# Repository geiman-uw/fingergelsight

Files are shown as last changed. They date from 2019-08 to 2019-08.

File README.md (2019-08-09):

# Assistive Finger GelSight

Words about the thing

## Table of Contents

* [Manufacture](#manufacture)  
  * [Supplies required](#supplies)  
  * [Core procedure](#coreprocedure)  
  * [Electronics procedure](#electronicsprocedure)  
  * [Assembly and installation](#aandi)  
* [Usage](#usage)
* [Capabilities](#capabilities)

## Manufacture

#### Supplies required<a name="supplies"/>
###### Chemicals
* Ease Release 200
* Silicones, Inc. XP-565
* Yellow Print-On Silicone Ink
* Print-On Silicone Ink diluent
* ?mm transparent acrylic
* Gray Print-On Silicone Ink
* Acrylic glue
<!--* Silicone glue-->
###### Other supplies
* Clear PLA 3D printer filament
* Petri dishes
* Pour boats
* Popsicle mixing sticks
* Pipets
* Needle-tip bottle

#### Equipment required
* Fume hood *(if available)*
* Vacuum chamber
* Toaster oven
* 3D printer
* Laser cutter

A vacuum chamber and toaster oven have been stored in ECE B031 ("silicone lab"), but check with the current project owner for the current location. There are multiple makerspaces at UW which have 3D printers and laser cutters; the two most accessible are the MILL in McCarty Hall and CoMotion Makerspace in Fluke Hall.

### Core procedure<a name="coreprocedure"/>  
Notes:
* You may find it most efficient to make 4-8 cores at a time with this procedure.
* Mix silicones in a pour boat using a popsicle stick. Use popsicle sticks to portion more viscous materials such as silicone base, and pipets to portion less viscous materials such as activator and diluent. Never use the same pipet or popsicle stick for different materials. 
* PLA parts shrink when exposed to heat. If you plan to modify the core, make your part approximately 5% bigger than the intended final size in order to account for this.
#### 1. Silicone lab
* __Cast transparent gel silicone__: After ensuring petri dish is free of dust, spray petri dish with Ease Release 200. Mix 17-18g XP-565, then pour 15g into dish. Vacuum until no bubbles remain, then heat on warm for 10 min.
* __Add yellow layer__: Starting with a 1g of yellow Silicone Ink, mix in a 1:10:60 activator:ink:diluent ratio. The resulting mixture should be approximately the consistency of chocolate milk. Pour in a thin even layer over the XP-565 petri dish. The layer should be as thin as possible, so you will not use all of the yellow silicone. Heat the dish on warm for 15 min.

#### 2. Makerspace
All production files can be found in `finger_gelsight_production`.
* **Print parts**: Print `gelsight_shell.stl` and `gelsight_piece.stl` in opaque PLA. Print `gelsight_corefilled_103.stl` open side up in clear PLA with 0.2mm layer height, raft, and no support.
* **Laser cut acrylic**: Laser cut `gelsight_corefilled_acrylic.stl` with vector set to *8s 100p 100f*.
* **Laser cut and engrave gel**: Remove transparent/yellow silicone from petri dish and place yellow-side up in laser cutter. Laser cut `gelsight_gelpattern_5x14.ai` with raster set to *11s 4p 50f* and vector set to *5s 75p 50f*.

#### 3. Silicone lab
* __Cast transparent core silicone__: Mix enough XP-565 to fill the prepared cores, and vacuum in pour boat until most bubbles are gone. 
* __Glue acrylic into core__: Using a needle-tip bottle, apply acrylic glue to the inside of the cores and place acrylic. Make sure the glue gets all the way around the edges, otherwise the silicone will seep past the acrylic and obstruct the camera lens later.
* __Fill core with silicone__: Carefully fill each core with silicone (at or below edge; do not overflow) and vacuum until no bubbles remain, then heat on warm for 5 min. 
* __Add protection layer__: Starting with 0.5g of gray Silicone Ink, mix in a 1:10:40 activator:ink:diluent ratio. The resulting mixture should be somewhat thicker than chocolate milk. Cover the bottom of each cut-out gel with electrical tape, making sure there are no bubbles where gray silicone could seep under the gel. Place dot-side up in a petri dish. Using a pipet, cover each gel in gray silicone mix, making sure all untaped sides are covered. 
* __Attach gel to core__: Once cores have cooled, spread a thin layer of mixed XP-565 on each core. Gently place gel on XP-565 layer, being careful to avoid introducing bubbles. Heat on warm for 5 min.

### Electronics procedure<a name="electronicsprocedure"/>
Wire two Adafruit LED sequins in parallel. Cut and strip a USB cable and solder each LED lead to the appropriate USB cable wire.
[images]

### Assembly and installation<a name="aandi"/>
Tap core and shell holes with M2 tap. Attach LEDs to core with transperent double sided tape. Screw core into shell. Attach camera to core with double sided tape, being careful not to force the lens into the hole. Tape wires to shell to provide more stability.

On Kinova hand remove original KG-2 distal phalanxes, being careful not to stretch rubber excessively. Place Finger GelSight and screw in shell piece. Continue as if installing original Kinova distal phalanx. Plug both USBs into the wrist controller. The fingers are now ready to use.

## Usage

## Capabilities

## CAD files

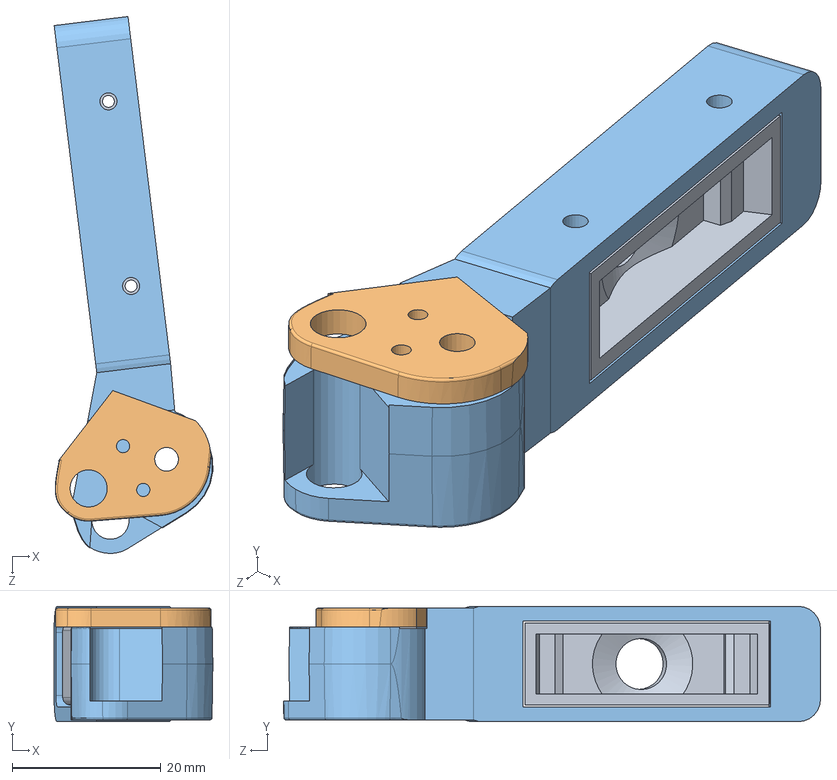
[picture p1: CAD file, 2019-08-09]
finger_gelsight_assembly/gripper_fingerassembly.sldasm
21.3 x 15.5 x 72.2 mm
gelsight_shell
gelsight_piece
gelsight_corefilled

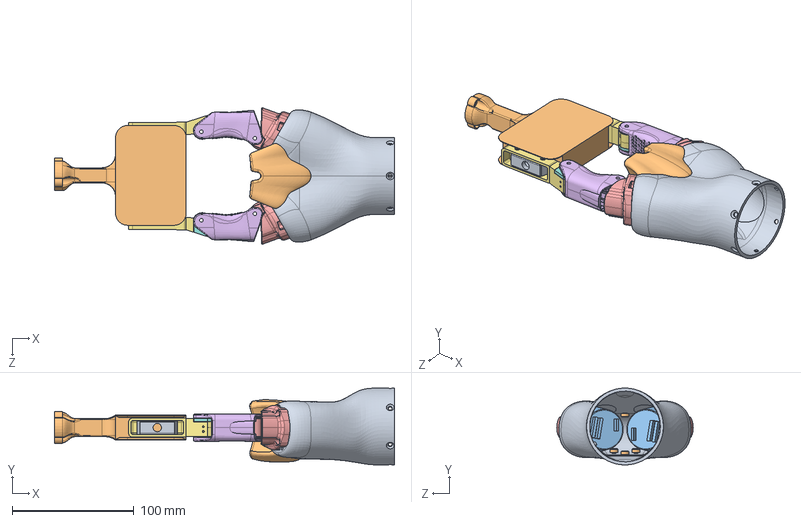
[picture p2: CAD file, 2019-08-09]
finger_gelsight_assembly/gripper_assembly.SLDASM
278.9 x 63.0 x 112.0 mm
gripper_handshell
gripper_handfront
actuator_dummy x 2
actuator_cup x 2
gripper_fingershroud x 2
gripper_middlephalanx x 2
gelsight_shell x 2
gelsight_piece x 2
gelsight_corefilled x 2
forkholder

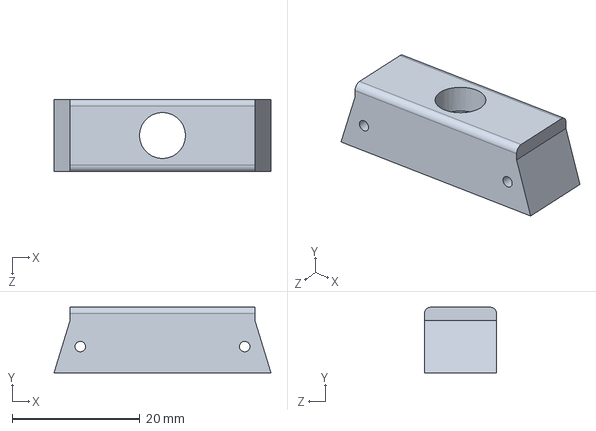
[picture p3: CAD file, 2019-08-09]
finger_gelsight_production/gelsight_corefilled_103.SLDPRT
34.0 x 10.3 x 11.3 mm

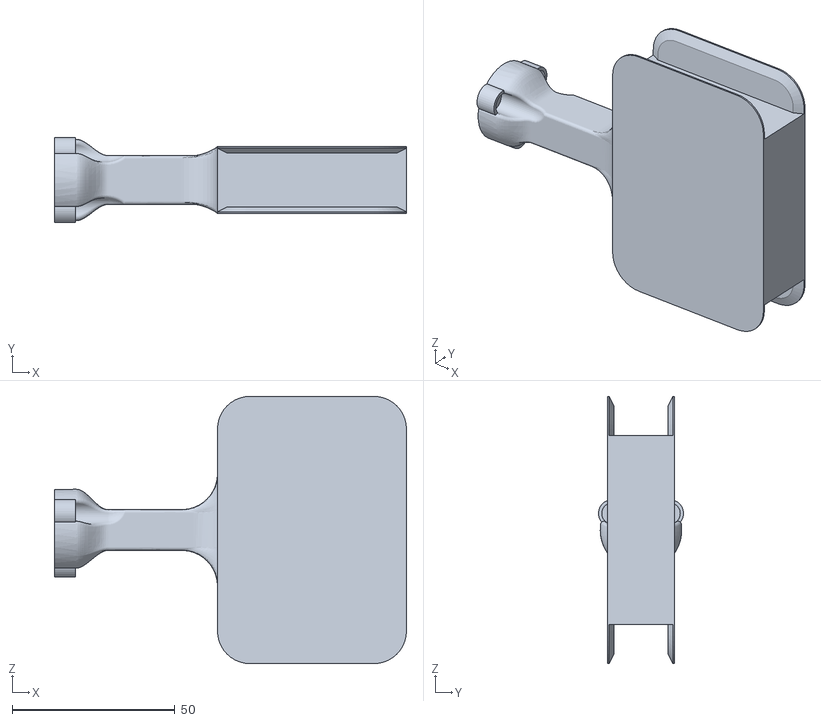
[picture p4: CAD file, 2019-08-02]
finger_gelsight_production/forkholder.STL
108.0 x 26.1 x 82.0

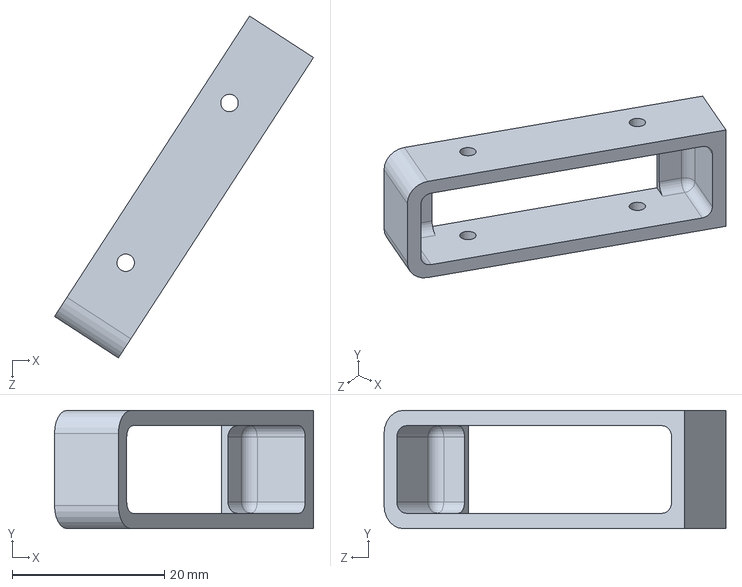
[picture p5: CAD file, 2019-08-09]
finger_gelsight_assembly/Body5.sldprt
34.0 x 15.5 x 44.9 mm

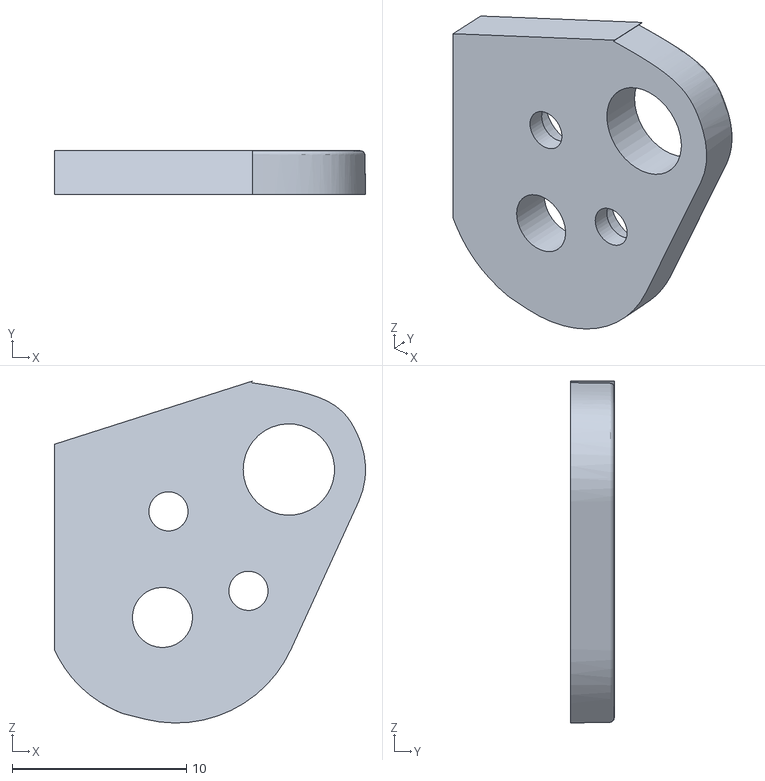
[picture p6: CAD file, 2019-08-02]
finger_gelsight_production/gelsight_piece.STL
17.9 x 2.50 x 19.7

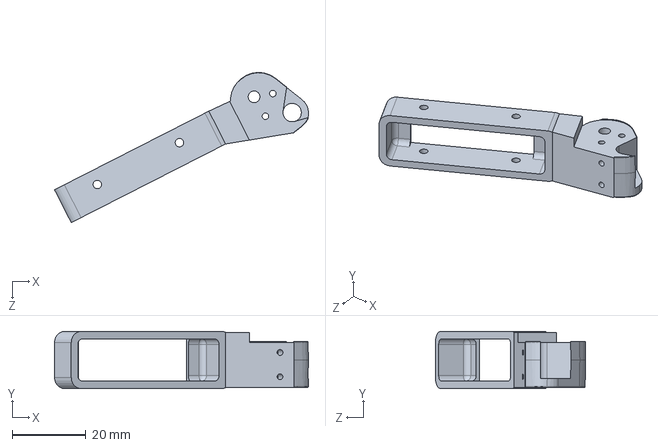
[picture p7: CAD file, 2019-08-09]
finger_gelsight_assembly/gelsight_shell.sldprt
68.9 x 15.5 x 40.8 mm

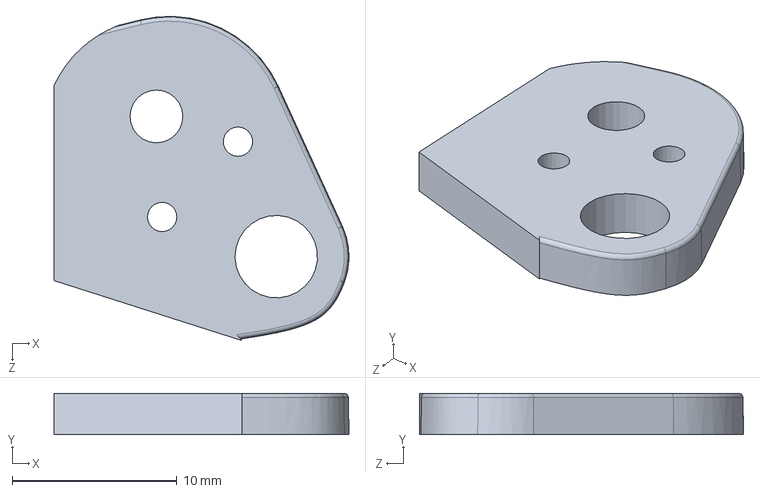
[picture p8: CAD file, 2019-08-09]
finger_gelsight_assembly/gelsight_piece.sldprt
17.9 x 2.50 x 19.6 mm

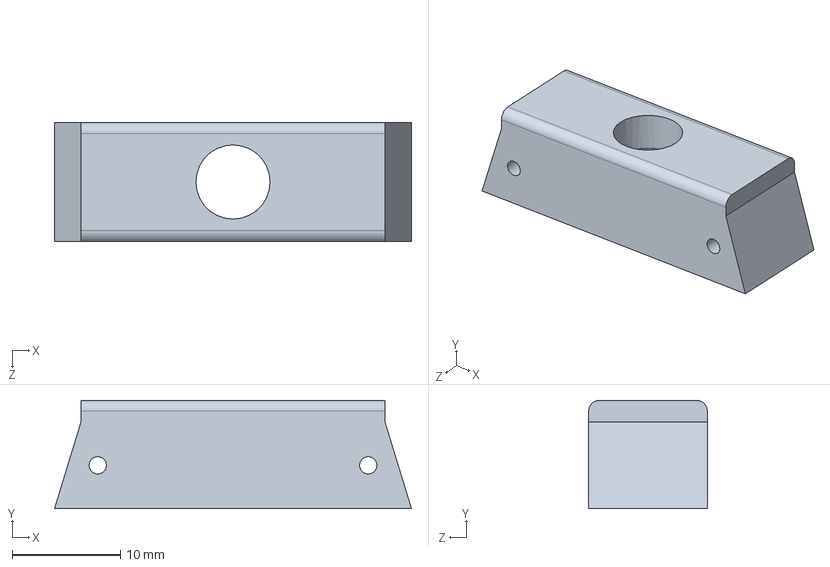
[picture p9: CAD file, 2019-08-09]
finger_gelsight_assembly/gelsight_corefilled.SLDPRT
33.0 x 10.0 x 11.0 mm

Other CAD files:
finger_gelsight_assembly/gripper_linearactuator.sldasm
finger_gelsight_assembly/MI 0000 0002 - 1.0.0.0005_simple_molded_version.sldprt
finger_gelsight_production/gelsight_shell.STL
finger_gelsight_assembly/MI 1502 0001 - 1.0.0.0002_simple_D‚faut.sldprt
finger_gelsight_assembly/forkholder.sldprt
finger_gelsight_assembly/gripper_handshell.sldprt
finger_gelsight_assembly/gripper_fingershroud.sldprt
finger_gelsight_assembly/actuator_dummy.sldprt
finger_gelsight_assembly/gripper_handfront.sldprt
finger_gelsight_assembly/actuator_cup.sldprt
finger_gelsight_assembly/gripper_middlephalanx.sldprt
finger_gelsight_production/gelsight_corefilled_103.STL

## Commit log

2019-08-02 add CAD, STL, and AI files for finger manufacture
    [actuator_cup.sldprt, actuator_dummy.sldprt, forkholder.STL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]
2019-08-09 Update CAD and production files
    [Body5.sldprt, MI 0000 0002 - 1.0.0.0005_simple_molded_version.sldprt, MI 1502 0001 - 1.0.0.0002_simple_D‚faut.sldprt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]
